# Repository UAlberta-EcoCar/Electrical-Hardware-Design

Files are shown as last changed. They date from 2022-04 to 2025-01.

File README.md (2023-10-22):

# Electrical-2022-Design-Hardware
## Relay-Board - Nicholas Semmens
Contains the hardware design for the upcoming prototype vehicle

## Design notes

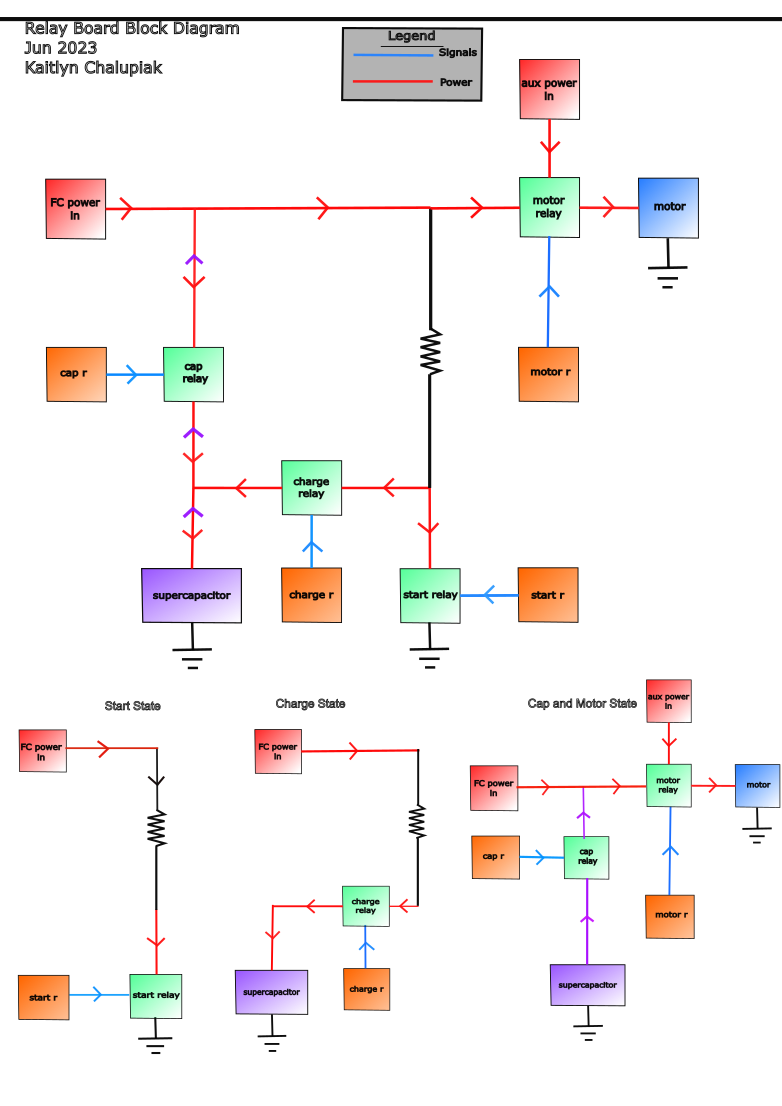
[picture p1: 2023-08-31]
Relay-Board_2023_Lucy_V1/Relay_Board_Lucy_V1/EcoCar_RelayBoard_BlockDiagram7_V3frfr.png

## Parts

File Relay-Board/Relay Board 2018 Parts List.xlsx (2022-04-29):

Relay Board Digikey List 2018
Part Description | Quantity | Store # | Store
8AWG Wire-to-Board Connector | 10 | 732-3204-ND
Switch (Voltage Divider) | 3 | EG1903-ND
Resistor 0603 (10.5k ohm) | 3 | P10.5KDBCT-ND
Resistor 0603 (768 ohm) | 3 | P768HCT-ND
Resistor 0603 (1.5k ohm) | 3 | P1.5KDBCT-ND
TVS Diode | 2 | P6KE15A-E3/54GICT-ND
RJ-11 | 3 | A119660-ND
RJ-45 | 2 | A122645-ND
Power Board Relay | 1 | CLA394-ND
Current Sensor (50A) | 2 | 620-1541-5-ND
Current Sensor (100A) | 1 | 620-1544-5-ND
Capacitor 0603 (0.1uF) | 3 | 399-1096-1-ND
Resistor 0603 (10k ohm) | 4 | RHM10KDCT-ND
Resistor 0603 (470 ohm) | 4 | RHM470DCT-ND
Photocoupler | 4 | H11L1-MQT-ND
P-MOS | 4 | DMP3056L-7DICT-ND
Flyback Diode | 4 | MUR420RLGOSCT-ND
Relay Socket | 4 | PB232-ND
90A Relay | 2 | 255-5246-ND

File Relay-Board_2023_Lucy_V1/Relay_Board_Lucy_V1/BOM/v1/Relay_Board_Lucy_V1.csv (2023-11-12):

Source: | C:\Users\Nicks_PC\Documents\virtDesk\Electrical-Hardware-Design\Relay-Board_2023_Lucy_V1\Relay_Board_Lucy_V1\Relay_Board_Lucy_V1.kicad_sch
Date: | 11/12/2023 2:34:30 PM
Tool: | Eeschema 7.0.2
Generator: | C:\Program Files\KiCad\7.0\bin\scripting\plugins/bom_csv_grouped_by_value.py
Component Count: | 113
Collated Components:
Item | Qty | Reference(s) | Value | LibPart | Footprint | Datasheet | DNP | Desc | Part#
1 | 17 | C1, C2, C5, C6, C7, C9, C10, C11, C13, C15, C16, C17, C19, C20, C21, C23, C24 | 100n | Device:C_Small | Capacitor_SMD:C_0603_1608Metric | https://datasheet.lcsc.com/lcsc/2304140030_FH--Guangdong-Fenghua-Advanced-Tech-0603B104K101NT_C88219.pdf |  |  | C88219
2 | 5 | C3, C4, C8, C14, C22 | 1u | Device:C_Small | Capacitor_SMD:C_0603_1608Metric | https://datasheet.lcsc.com/lcsc/2304140030_Murata-Electronics-GRM188R71C105KE15D_C77049.pdf |  |  | C77049
3 | 2 | C12, C18 | 4u7 | Device:C_Small | Capacitor_SMD:C_0603_1608Metric | https://datasheet.lcsc.com/lcsc/2304140030_FH--Guangdong-Fenghua-Advanced-Tech-0603B475K100NT_C108342.pdf |  | Desc: ESR < 1 | C108342
4 | 3 | D2, D10, D11 | AM23ESGW | Device:LED_Dual_AAK | Package_TO_SOT_SMD:SOT-23-3 | https://www.kingbrightusa.com/images/catalog/SPEC/AM23ESGW.pdf |  |  | 754-1634-6-ND
5 | 1 | D3 | STPS5045SG-TR | Device:D_Schottky_AKA | Package_TO_SOT_SMD:TO-263-2 | https://www.st.com/content/ccc/resource/technical/document/datasheet/65/29/29/69/d0/df/47/9c/DM00049255.pdf/files/DM00049255.pdf/jcr:content/translations/en.D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 |  |  | 497-13279-1-ND
6 | 6 | D4, D5, D6, D7, D8, D9 | BZX84-C3V3,215 | Device:D_Zener_Dual_CommonCathode_AAK | Package_TO_SOT_SMD:SOT-23-3 | https://assets.nexperia.com/documents/data-sheet/BZX84_SER.pdf |  |  | C85087
7 | 4 | D12, D13, D14, D15 | SD0805S020S1R0 | Device:D_Schottky | Diode_SMD:D_0805_2012Metric_Pad1.15x1.40mm_HandSolder | https://datasheets.kyocera-avx.com/schottky.pdf |  |  | 478-7800-1-ND
8 | 1 | FB1 | 300R | Device:FerriteBead_Small | Inductor_SMD:L_1206_3216Metric | https://www.vishay.com/docs/34023/ilb1206.pdf |  |  | 541-2283-1-ND
9 | 4 | H1, H2, H3, H4 | MountingHole | Mechanical:MountingHole | MountingHole:MountingHole_3.2mm_M3 | ~ |  |  | N/A
10 | 2 | J1, J10 | STD_PWR_HEADER | RB_PARTS:STD_PWR_HEADER | RB_FTP:STD_PWR_HEADER | https://www.molex.com/pdm_docs/ps/PS-43045.pdf |  |  | WM1791-ND
11 | 4 | J2, J3, J4, J5 | VP0265540000G | RB_PARTS:VP0265540000G | RB_FTP:CONN_VP0265x4xxxxG_AMP | https://mm.digikey.com/Volume0/opasdata/d220001/medias/docus/3772/8VP0003.pdf |  |  | VP0265540000G-ND
12 | 1 | J7 | USB_B_Micro | Connector:USB_B_Micro | RB_FTP:USB_Micro-B_Wuerth_629105150521 | https://www.we-online.com/katalog/datasheet/629105150521.pdf |  |  | 732-5960-1-ND
13 | 1 | J9 | DE9_Receptacle_MountingHoles | Connector:DE9_Receptacle_MountingHoles | Connector_Dsub:DSUB-9_Female_Horizontal_P2.77x2.84mm_EdgePinOffset7.70mm_Housed_MountingHolesOffset9.12mm | ~ |  |  | N/A
14 | 1 | JP3 | SolderJumper_2_Open | Jumper:SolderJumper_2_Open | Jumper:SolderJumper-2_P1.3mm_Open_TrianglePad1.0x1.5mm | ~ |  |  | N/A
15 | 2 | K1, K2 | HE1AN-P-DC12V-Y5 | RB_PARTS:HE1AN-W-DC12V-Y6 | RB_FTP:HE1AN-P-DC12V-Y5 | https://api.pim.na.industrial.panasonic.com/file_stream/main/fileversion/276 |  |  | 255-2777-ND
16 | 2 | K3, K4 | J115F11CH12VDCS61.5 | RB_PARTS:T9AV5L12-12 | RB_FTP:J115F11CH12VDCS61.5 | http://www.te.com/commerce/DocumentDelivery/DDEController?Action=showdoc |  |  | 2449-J115F11CH12VDCS61.5-ND
17 | 1 | Q1 | SI2302A-TPMSCT-ND | Device:Q_NMOS_GSD | Package_TO_SOT_SMD:SOT-23-3 | https://www.mccsemi.com/pdf/Products/SI2302A(SOT-23).pdf |  |  | SI2302A-TPMSCT-ND
18 | 4 | Q2, Q3, Q6, Q7 | FMMT491ATA | Device:Q_NPN_BEC | Package_TO_SOT_SMD:SOT-23-3 | https://www.diodes.com/assets/Datasheets/FMMT491A.pdf |  |  | C110504
19 | 1 | R1 | 160 | Device:R_Small | Resistor_SMD:R_0603_1608Metric | ~ |  |  | C245189
20 | 2 | R2, R4 | 2.2M | Device:R_Small | Resistor_SMD:R_0603_1608Metric | https://datasheet.lcsc.com/lcsc/2208261700_VO-SCR0603F2M2_C5140271.pdf |  |  | C5140271
21 | 1 | R3 | 953k | Device:R_Small | Resistor_SMD:R_0603_1608Metric | https://www.yageo.com/upload/media/product/productsearch/datasheet/rchip/PYu-RC_Group_51_RoHS_L_12.pdf |  |  | 311-953KHRCT-ND
22 | 1 | R5 | 549k | Device:R_Small | Resistor_SMD:R_0603_1608Metric | https://www.yageo.com/upload/media/product/app/datasheet/rchip/pyu-rc_group_51_rohs_l.pdf |  |  | 311-549KHRCT-ND
23 | 1 | R6 | 11.5k | Device:R_Small | Resistor_SMD:R_0603_1608Metric | https://datasheet.lcsc.com/lcsc/2304140030_Walsin-Tech-Corp-WR06X1152FTL_C168277.pdf |  |  | C168277
24 | 4 | R7, R11, R12, R20 | 100k | Device:R_Small | Resistor_SMD:R_0603_1608Metric | https://datasheet.lcsc.com/lcsc/2211251200_Ever-Ohms-Tech-TR0603D100KP0550Z_C5250829.pdf |  |  | C5250829
25 | 1 | R8 | 150 | Device:R_Small | Resistor_SMD:R_0603_1608Metric | https://datasheet.lcsc.com/lcsc/2206010130_UNI-ROYAL-Uniroyal-Elec-0603WAF1500T5E_C22808.pdf |  |  | C22808
26 | 3 | R9, R10, R19 | 417k | Device:R_Small | Resistor_SMD:R_0603_1608Metric | https://www.koaspeer.com/pdfs/RN73H.pdf |  |  | 2019-RN73H1JTTD4173C25CT-ND
27 | 3 | R13, R14, R17 | 50k | Device:R_Small | Resistor_SMD:R_0603_1608Metric | https://www.yageo.com/upload/media/product/productsearch/datasheet/rchip/PYu-RT_1-to-0.01_RoHS_L_15.pdf |  |  | 13-RT0603BRD0750KLCT-ND
28 | 3 | R15, R16, R18 | 200k | Device:R_Small | Resistor_SMD:R_0603_1608Metric | https://datasheet.lcsc.com/lcsc/2206010045_UNI-ROYAL-Uniroyal-Elec-0603WAF2003T5E_C25811.pdf |  |  | C25811
29 | 2 | R21, R23 | 140 | Device:R_Small | Resistor_SMD:R_0603_1608Metric | https://datasheet.lcsc.com/lcsc/2304140030_FH--Guangdong-Fenghua-Advanced-Tech-RS-03K1400FT_C304700.pdf |  |  | C304700
30 | 2 | R22, R24 | 130 | Device:R_Small | Resistor_SMD:R_0603_1608Metric | https://datasheet.lcsc.com/lcsc/2304140030_TA-I-Tech-RMS06FT1300_C209032.pdf |  |  | C209032
31 | 1 | R25 | 10k | Device:R_Small | Resistor_SMD:R_0603_1608Metric | https://datasheet.lcsc.com/lcsc/2206010045_UNI-ROYAL-Uniroyal-Elec-0603WAF1002T5E_C25804.pdf |  |  | C25804
32 | 4 | R27, R29, R31, R33 | 249 | Device:R_Small | Resistor_SMD:R_0603_1608Metric | https://datasheet.lcsc.com/lcsc/2304140030_Viking-Tech-ARG03FTC2490_C217903.pdf |  |  | C217903
33 | 1 | R34 | 120 | Device:R_Small | Resistor_SMD:R_0603_1608Metric | https://datasheet.lcsc.com/lcsc/2206010130_UNI-ROYAL-Uniroyal-Elec-0603WAF1200T5E_C22787.pdf | DNP |  | C22787
34 | 4 | R35, R36, R37, R38 | 422 | Device:R_Small | Resistor_SMD:R_0603_1608Metric | https://datasheet.lcsc.com/lcsc/2206010130_UNI-ROYAL-Uniroyal-Elec-0603WAF2200T5E_C22962.pdf |  |  | C22962
35 | 2 | SW1, SW2 | PTS815 SJM 250 SMTR LFS | Switch:SW_Push_45deg | Button_Switch_SMD:SW_SPST_PTS810 | https://datasheet.lcsc.com/lcsc/2106070033_C-K-PTS815SJM250SMTRLFS_C2689510.pdf |  |  | C2689510
36 | 2 | TP1, TP2 | TestPoint_Alt | Connector:TestPoint_Alt | TestPoint:TestPoint_Pad_1.0x1.0mm | ~ |  |  | N/A
37 | 2 | U1, U6 | ACS770LCB-050U-PFF | Sensor_Current:ACS770xCB-050B-PFF | RB_FTP:Allegro_CB_PFF_Adjusted | https://www.allegromicro.com/~/media/Files/Datasheets/ACS770-Datasheet.ashx |  |  | 620-1542-5-ND
38 | 1 | U2 | ACS770LCB-050B-PFF | Sensor_Current:ACS770xCB-050B-PFF | RB_FTP:Allegro_CB_PFF_Adjusted | https://www.allegromicro.com/~/media/Files/Datasheets/ACS770-Datasheet.ashx |  |  | 620-1541-5-ND
39 | 1 | U3 | MAX14572 | FCC_PARTS:MAX14572 | Package_SO:TSSOP-14-1EP_4.4x5mm_P0.65mm | https://www.analog.com/media/en/technical-documentation/data-sheets/MAX14571-MAX14573.pdf |  |  | MAX14572EUD+TCT-ND
40 | 2 | U4, U5 | TSV914IPT | RB_PARTS:TSV914IPT | Package_SO:TSSOP-14_4.4x5mm_P0.65mm | https://www.st.com/content/ccc/resource/technical/document/datasheet/68/e5/70/49/1a/0d/47/dd/CD00127596.pdf/files/CD00127596.pdf/jcr:content/translations/en.C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 |  |  | C83262
41 | 1 | U7 | LD39050PU33R | FCC_PARTS:LD39050PU33R | Package_DFN_QFN:DFN-6-1EP_3x3mm_P0.95mm_EP1.7x2.6mm | https://www.st.com/content/ccc/resource/technical/document/datasheet/12/43/cc/93/21/f6/41/66/CD00227527.pdf/files/CD00227527.pdf/jcr:content/translations/en.C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 |  |  | C132827
42 | 4 | U8, U11, U12, U13 | EL3H7(B)(TA)-VG | RB_PARTS:EL3H7(B)(TA)-VG | RB_FTP:SOIC_BTA-VG_EVS | https://everlightamericas.com/index.php?controller=attachment&id_attachment=2584 |  |  | C2891578
43 | 1 | U9 | MCP2542FD-E/SN | FCC_PARTS:MCP2542FD | Package_SO:SOIC-8_3.9x4.9mm_P1.27mm | https://ww1.microchip.com/downloads/aemDocuments/documents/APID/ProductDocuments/DataSheets/MCP2542FD-MCP2542WFD-4WFD-Data-Sheet-DS20005514C.pdf |  |  | C220598
44 | 1 | U10 | STM32F446RETx | MCU_ST_STM32F4:STM32F446RETx | Package_QFP:LQFP-64_10x10mm_P0.5mm | https://www.st.com/resource/en/datasheet/stm32f446re.pdf |  |  | C69336
45 | 1 | X1 | OXETDLJANF-8MHZ | RB_PARTS:OXETDLJANF-8MHZ | Crystal:Crystal_SMD_3225-4Pin_3.2x2.5mm | https://datasheet.lcsc.com/lcsc/2304140030_TAITIEN-Elec-OXETDLJANF-8-000000MHZ_C558766.pdf |  | 3.3V ±25ppm 8MHz SMD3225-4P Oscillators ROHS | C558766

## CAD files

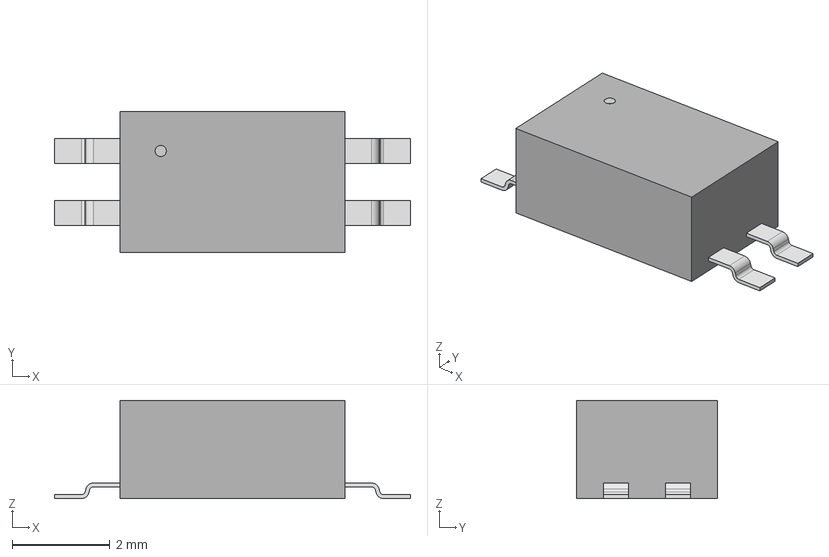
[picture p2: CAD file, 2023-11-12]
Relay-Board_2023_Lucy_V1/Relay_Board_Lucy_V1/SYM&FTP/3D/SOIC__B__TA_-VG_EVS.step
7.29 x 2.90 x 2.01 mm

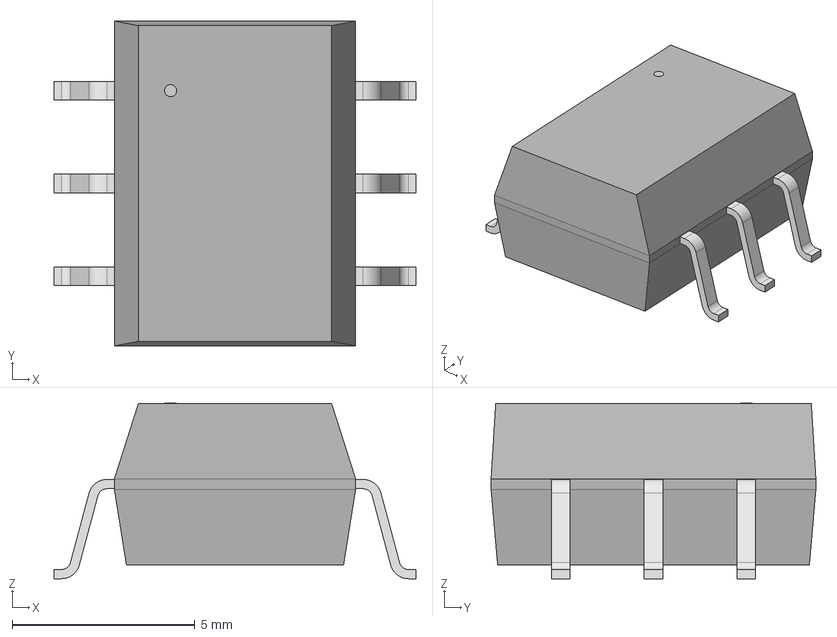
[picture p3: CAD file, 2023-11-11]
Relay-Board_2023_Lucy_V1/Relay_Board_Lucy_V1/SYM&FTP/3D/PDIP6_646BY_ONS.step
9.91 x 8.89 x 4.80 mm

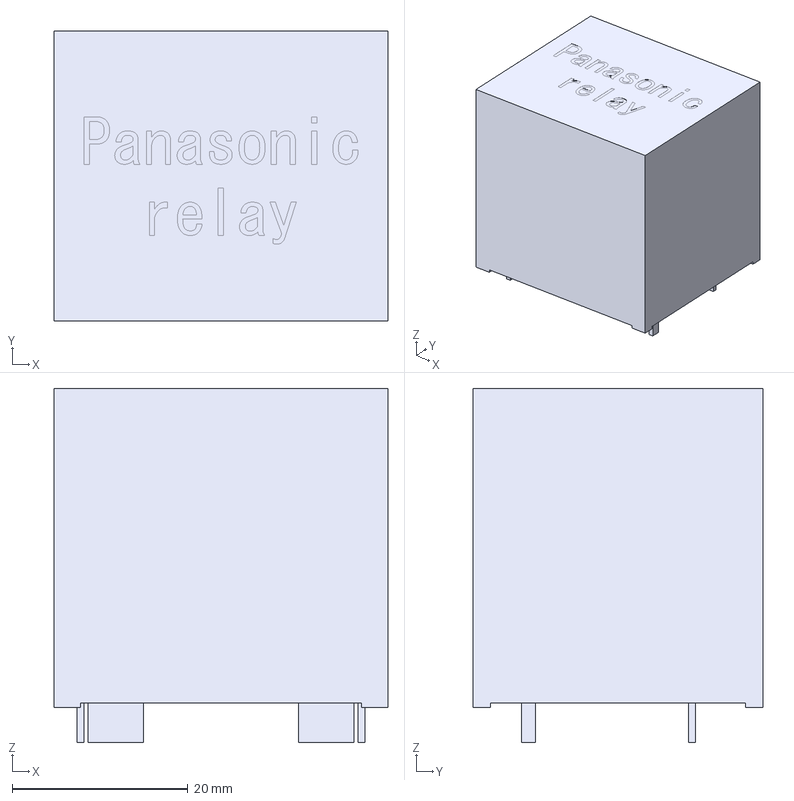
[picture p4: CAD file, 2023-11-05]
Relay-Board_2023_Lucy_V1/Relay_Board_Lucy_V1/SYM&FTP/3D/ahe32x5n.step
38.0 x 33.0 x 40.3 mm

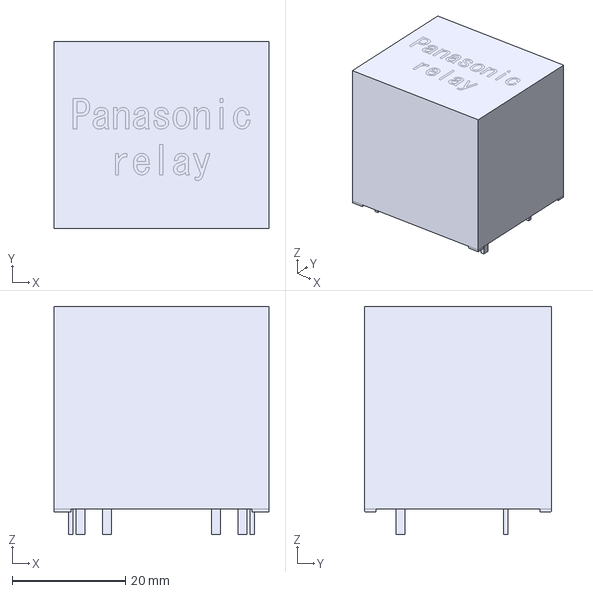
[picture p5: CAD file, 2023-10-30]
Relay-Board_2023_Lucy_V1/Relay_Board_Lucy_V1/SYM&FTP/3D/ahe4291.step
38.0 x 33.0 x 40.3 mm

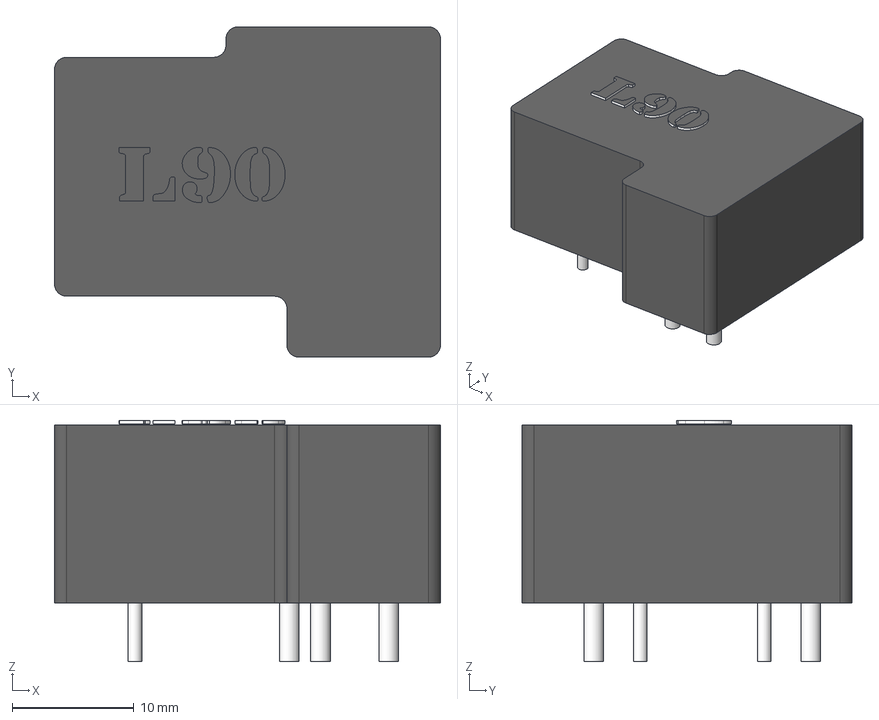
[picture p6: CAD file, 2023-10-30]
Relay-Board_2023_Lucy_V1/Relay_Board_Lucy_V1/SYM&FTP/3D/PTRH.step
31.7 x 27.1 x 19.8 mm

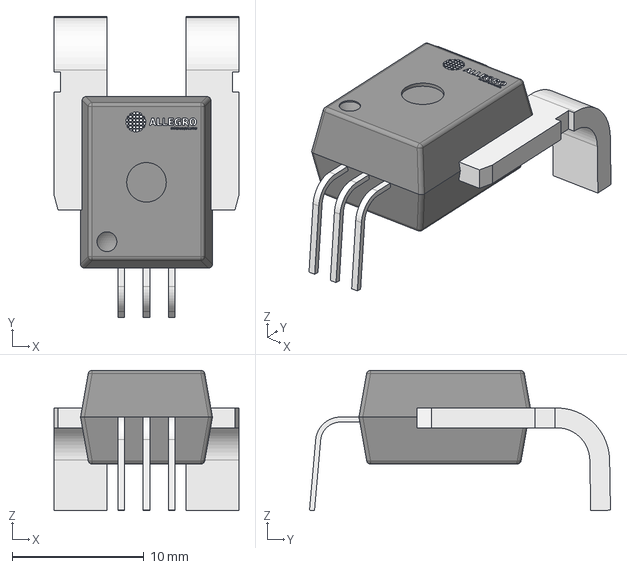
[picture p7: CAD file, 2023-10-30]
Relay-Board_2023_Lucy_V1/Relay_Board_Lucy_V1/SYM&FTP/3D/Allegro_MicroSystems_LLC_-_ACS770LCB-050U-PFF-T.step
14.0 x 22.8 x 10.6 mm

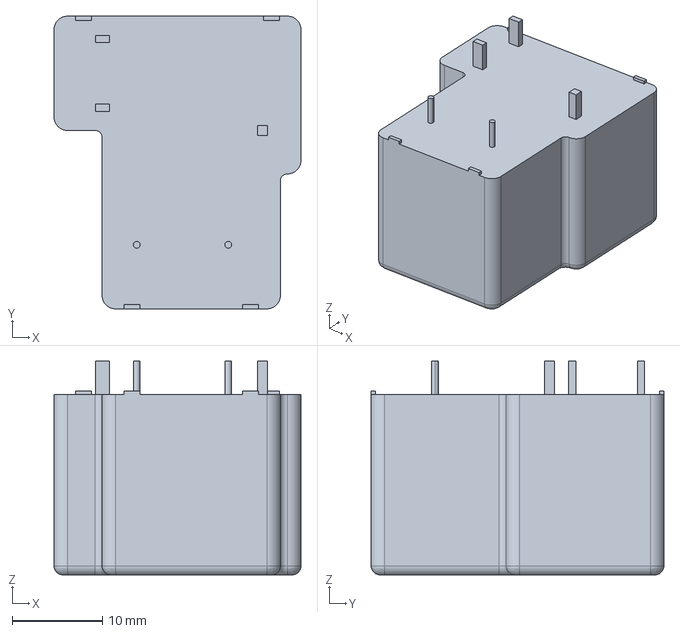
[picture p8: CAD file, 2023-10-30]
Relay-Board_2023_Lucy_V1/Relay_Board_Lucy_V1/SYM&FTP/3D/c-1423091-6-k-3d.stp
27.4 x 32.5 x 23.7 mm

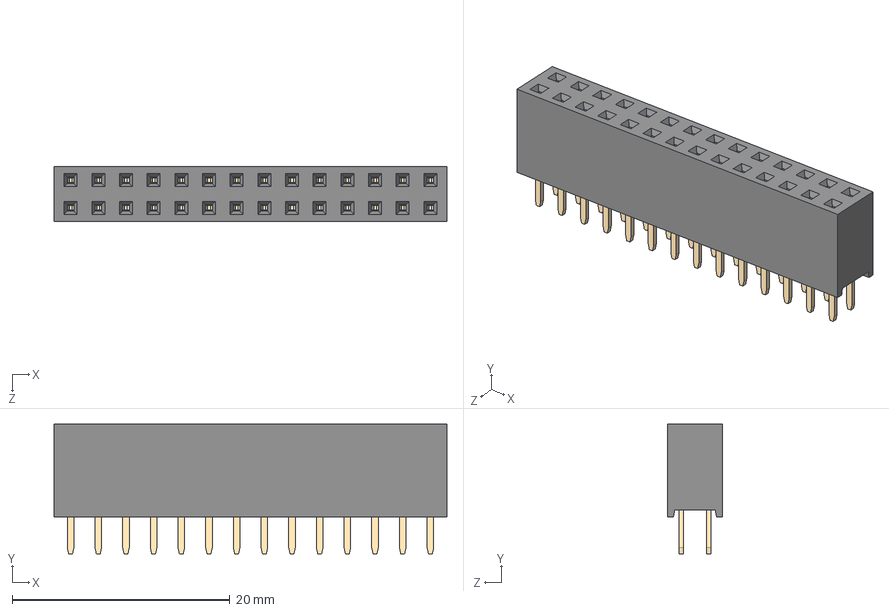
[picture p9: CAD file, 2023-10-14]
Relay-Board_2023_Lucy_V1/Relay_Board_Lucy_V1/SYM&FTP/3D/PPPC142LFBN-RC.STEP
36.1 x 11.9 x 5.08 mm
2 row tin body_14
2 row tin pins x 14

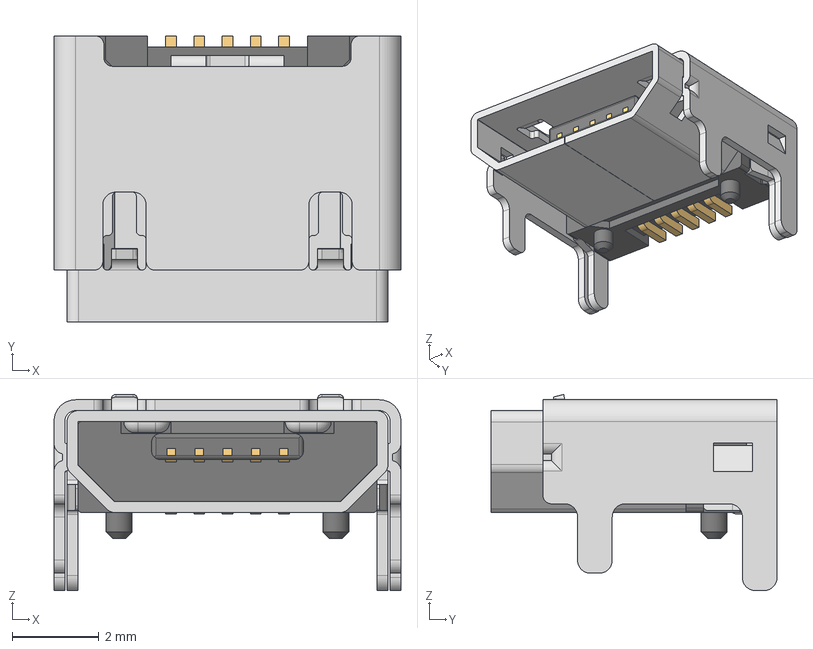
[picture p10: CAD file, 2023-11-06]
Relay-Board_2023_Lucy_V1/Relay_Board_Lucy_V1/SYM&FTP/3D/629105150521_Download_STP_629105150521_rev1.stp
8.00 x 6.60 x 4.52 mm
629105150521_Housing
629105150521_Pin1 x 4
629105150521_Pin2
629105150521_Shielding2
629105150521_Shielding

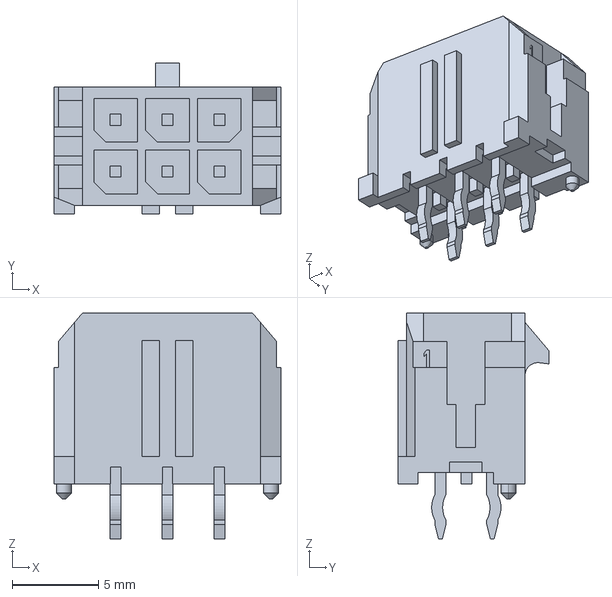
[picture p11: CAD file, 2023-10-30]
Relay-Board_2023_Lucy_V1/Relay_Board_Lucy_V1/SYM&FTP/3D/430450612.stp
13.2 x 8.77 x 13.1 mm

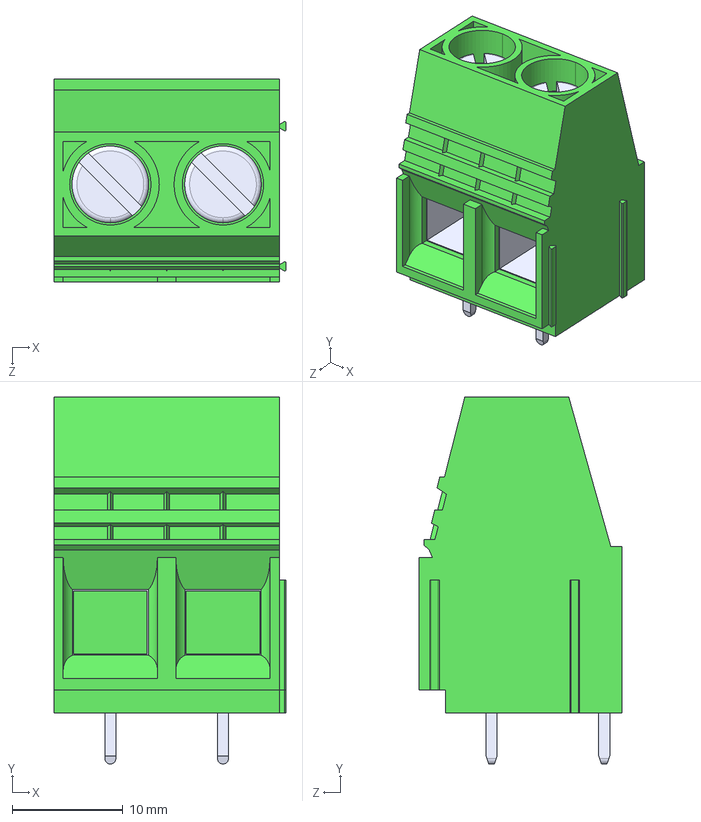
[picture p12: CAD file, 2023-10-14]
Relay-Board_2023_Lucy_V1/Relay_Board_Lucy_V1/SYM&FTP/3D/VP0265540000G.STEP
20.9 x 33.1 x 18.3 mm

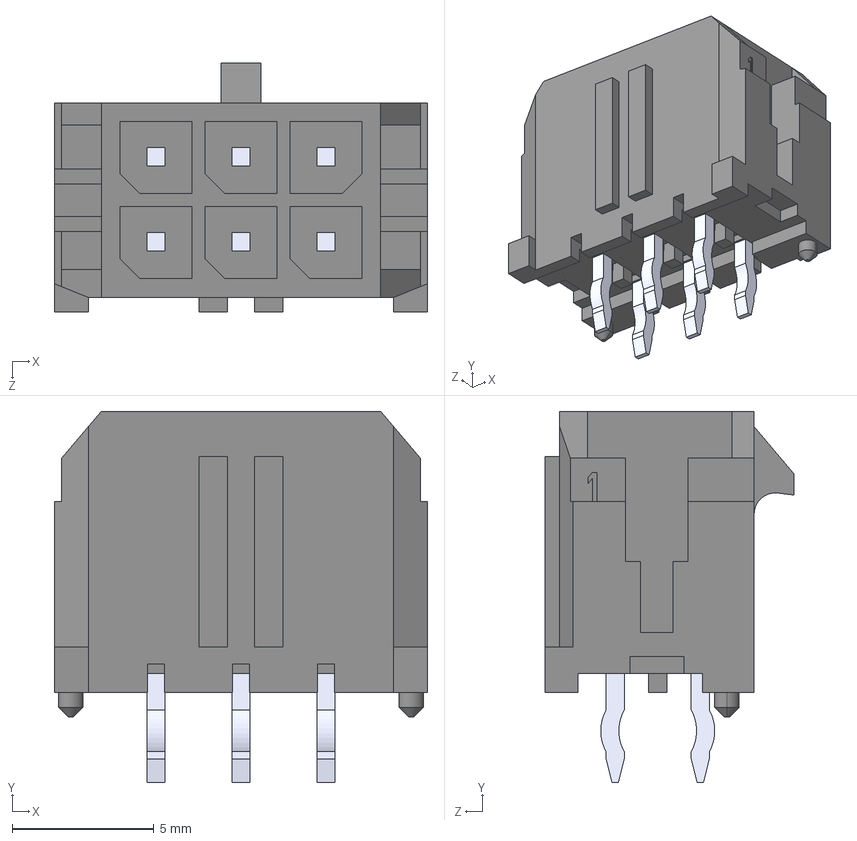
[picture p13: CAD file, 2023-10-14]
Relay-Board_2023_Lucy_V1/Relay_Board_Lucy_V1/SYM&FTP/3D/0430450612.step
13.2 x 13.1 x 8.77 mm

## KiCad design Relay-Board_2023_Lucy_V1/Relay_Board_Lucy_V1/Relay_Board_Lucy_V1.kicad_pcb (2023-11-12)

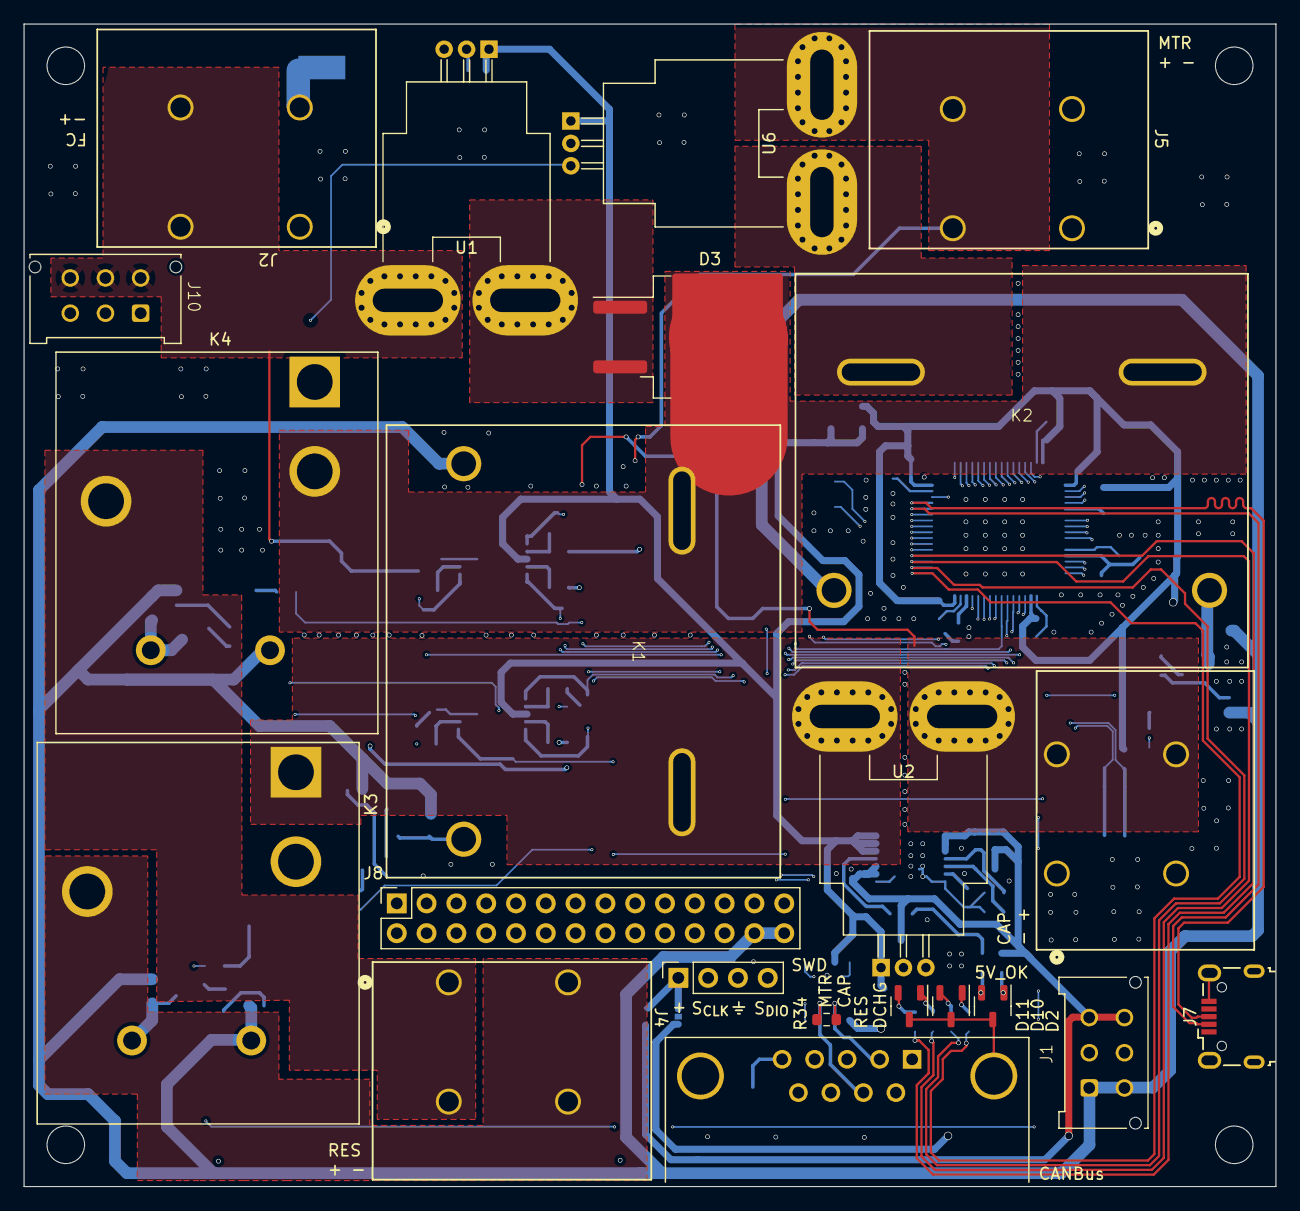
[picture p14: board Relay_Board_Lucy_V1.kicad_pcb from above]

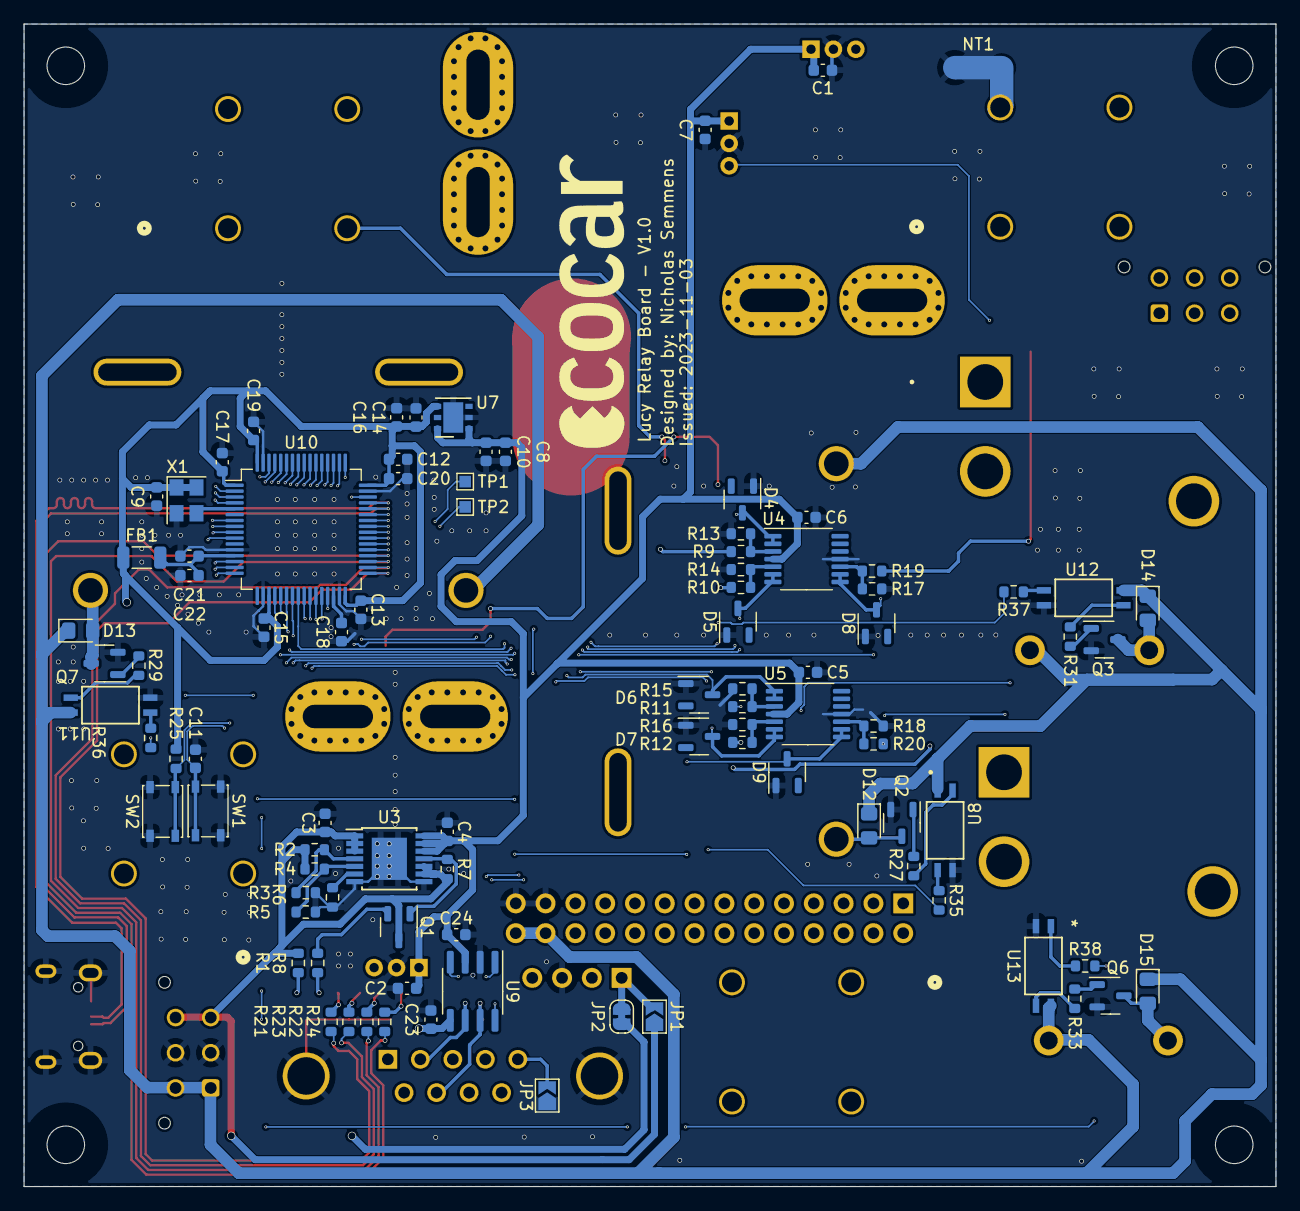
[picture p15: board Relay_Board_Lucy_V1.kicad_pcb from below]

Board: 4 copper layers, 106.7 x 99.1 mm, 118 parts (92 on the bottom side), 106 nets.

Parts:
C1, C2, C5, C6, C7, C9, C10, C11, C13, C15, C16, C17, C19, C20, C21, C23, C24: 100n; C_0603_1608Metric
C3, C4, C8, C14, C22: 1u; C_0603_1608Metric
C12, C18: 4u7; C_0603_1608Metric
D2, D10, D11: AM23ESGW; SOT-23-3
D3: STPS5045SG-TR; TO-263-2
D4, D5, D6, D7, D8, D9: BZX84-C3V3,215; SOT-23-3
D12, D13, D14, D15: SD0805S020S1R0; D_0805_2012Metric_Pad1.15x1.40mm_HandSolder
FB1: 300R; L_1206_3216Metric
H1, H2, H3, H4: MountingHole; MountingHole_3.2mm_M3
J1, J10: STD_PWR_HEADER
J2, J3, J4, J5: VP0265540000G; CONN_VP0265x4xxxxG_AMP
J6: SWD_HEADER; PinSocket_1x04_P2.54mm_Vertical
J7: USB_B_Micro; USB_Micro-B_Wuerth_629105150521
J8: Conn_02x14_Top_Bottom; PinSocket_2x14_P2.54mm_Vertical
J9: DE9_Receptacle_MountingHoles; DSUB-9_Female_Horizontal_P2.77x2.84mm_EdgePinOffset7.70mm_H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
JP1, JP3: SolderJumper_2_Open; SolderJumper-2_P1.3mm_Open_TrianglePad1.0x1.5mm
JP2: SolderJumper_2_Bridged; SolderJumper-2_P1.3mm_Bridged_RoundedPad1.0x1.5mm
K1, K2: HE1AN-P-DC12V-Y5
K3, K4: J115F11CH12VDCS61.5
NT1: NetTie_2; NetTie-2_SMD_Pad2.0mm
Q1: SI2302A-TPMSCT-ND; SOT-23-3
Q2, Q3, Q6, Q7: FMMT491ATA; SOT-23-3
R1: 160; R_0603_1608Metric
R2, R4: 2.2M; R_0603_1608Metric
R3: 953k; R_0603_1608Metric
R5: 549k; R_0603_1608Metric
R6: 11.5k; R_0603_1608Metric
R7, R11, R12, R20: 100k; R_0603_1608Metric
R8: 150; R_0603_1608Metric
R9, R10, R19: 417k; R_0603_1608Metric
R13, R14, R17: 50k; R_0603_1608Metric
R15, R16, R18: 200k; R_0603_1608Metric
R21, R23: 140; R_0603_1608Metric
R22, R24: 130; R_0603_1608Metric
R25: 10k; R_0603_1608Metric
R27, R29, R31, R33: 246; R_0603_1608Metric
R34: 120; R_0603_1608Metric
R35, R36, R37, R38: 422; R_0603_1608Metric
SW1, SW2: PTS815 SJM 250 SMTR LFS; SW_SPST_PTS810
TP1, TP2: TestPoint_Alt; TestPoint_Pad_1.0x1.0mm
U1, U6: ACS770LCB-050U-PFF; Allegro_CB_PFF_Adjusted
U2: ACS770LCB-050B-PFF; Allegro_CB_PFF_Adjusted
U3: MAX14572; TSSOP-14-1EP_4.4x5mm_P0.65mm
U4, U5: TSV914IPT; TSSOP-14_4.4x5mm_P0.65mm
U7: LD39050PU33R; DFN-6-1EP_3x3mm_P0.95mm_EP1.7x2.6mm
U8, U11, U12, U13: EL3H7(B)(TA)-VG; SOIC_BTA-VG_EVS
U9: MCP2542FD-E/SN; SOIC-8_3.9x4.9mm_P1.27mm
U10: STM32F446RETx; LQFP-64_10x10mm_P0.5mm
X1: OXETDLJANF-8MHZ; Crystal_SMD_3225-4Pin_3.2x2.5mm

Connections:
+3.3VA: C21.1, C22.1, FB1.2, U10.13 (VDDA)
+3V3: C9.1, C12.1, C13.1, C14.1, C15.1, C16.1, C17.1, C19.1, C20.1, C23.1, FB1.1, JP2.1 (A), R25.1, U7.4 (VO), U9.5 (VIO), U10.1 (VBAT), U10.19 (VDD), U10.32 (VDD), U10.48 (VDD), U10.64 (VDD), X1.1 (Tri-State), X1.4 (VDD)
+5V: C1.1, C2.1, C4.2, C5.1, C6.1, C7.1, C8.1, C10.1, C24.2, U1.1 (VCC), U2.1 (VCC), U3.12 (OUT), U3.13 (OUT), U3.14 (OUT), U4.4 (VCC+), U5.4 (VCC+), U6.1 (VCC), U7.1 (EN), U7.6 (VI), U9.3 (VDD)
/CAP Relay/V_{E}: R27.1, U8.3
/CAP+: J3.3, J3.4, R10.2, U2.4 (IP+)
/CAP_CURR: R12.2, U2.3 (VIOUT)
/FC+: J2.3, J2.4, J10.4 (12V), J10.5 (GND), J10.6 (5V), R19.2, U1.4 (IP+)
/FC_CURR: R11.2, U1.3 (VIOUT)
/MAIN_POWER_BUS: D3.2 (K), K1.1 (IN-), K2.4 (IN+), K4.2
/MCU/BOOT0: R25.2, SW2.2, U10.60 (BOOT0)
/MCU/CAN_H: J9.7, R34.2, U9.7 (CANH)
/MCU/CAN_L: J9.2, R34.1, U9.6 (CANL)
/MCU/CLK: U10.5 (PH0), X1.3 (OUT)
/MCU/PA0: J8.4, U10.14 (PA0)
/MCU/PA1: J8.2, U10.15 (PA1)
/MCU/PA2: J8.1, U10.16 (PA2)
/MCU/PA4: D8.3 (K), U4.8 (OUT3), U4.9 (IN3-), U10.20 (PA4)
/MCU/PA5: D9.3 (K), U5.8 (OUT3), U5.9 (IN3-), U10.21 (PA5)
/MCU/PA6: D5.3 (K), U4.6 (IN2-), U4.7 (OUT2), U10.22 (PA6)
/MCU/PA7: D7.3 (K), U5.6 (IN2-), U5.7 (OUT2), U10.23 (PA7)
/MCU/PA8: TP1.1, U10.41 (PA8)
/MCU/PA9: J8.21, U10.42 (PA9)
/MCU/PA10: J8.24, U10.43 (PA10)
/MCU/PA13: J6.4, U10.46 (PA13)
/MCU/PA14: J6.2, U10.49 (PA14)
/MCU/PA15: J8.17, U10.50 (PA15)
/MCU/PB0: R38.2, U10.26 (PB0)
/MCU/PB1: R37.2, U10.27 (PB1)
/MCU/PB2: R35.2, U10.28 (PB2)
/MCU/PB3: J8.14, U10.55 (PB3)
/MCU/PB4: J8.11, U10.56 (PB4)
/MCU/PB5: J8.12, U10.57 (PB5)
/MCU/PB6: J8.9, U10.58 (PB6)
/MCU/PB7: U9.8 (STBY), U10.59 (PB7)
/MCU/PB8: U9.4 (RXD), U10.61 (PB8)
/MCU/PB9: U9.1 (TXD), U10.62 (PB9)
/MCU/PB10: R36.2, U10.29 (PB10)
/MCU/PB12: R21.1, U10.33 (PB12)
/MCU/PB13: R22.2, U10.34 (PB13)
/MCU/PB14: R23.1, U10.35 (PB14)
/MCU/PB15: R24.2, U10.36 (PB15)
/MCU/PC0: J8.5, U10.8 (PC0)
/MCU/PC1: J8.6, U10.9 (PC1)
/MCU/PC2: J8.3, U10.10 (PC2)
/MCU/PC4: D4.3 (K), U4.1 (OUT1), U4.2 (IN1-), U10.24 (PC4)
/MCU/PC5: D6.3 (K), U5.1 (OUT1), U5.2 (IN1-), U10.25 (PC5)
/MCU/PC6: J8.20, U10.37 (PC6)
/MCU/PC7: J8.19, U10.38 (PC7)
/MCU/PC8: J8.22, U10.39 (PC8)
/MCU/PC9: TP2.1, U10.40 (PC9)
/MCU/PC10: J8.18, U10.51 (PC10)
/MCU/PC11: J8.15, U10.52 (PC11)
/MCU/PC12: J8.16, U10.53 (PC12)
/MCU/PC13: J8.10, U10.2 (PC13)
/MCU/PC14: J8.7, U10.3 (PC14)
/MCU/PC15: J8.8, U10.4 (PC15)
/MCU/PD2: J8.13, U10.54 (PD2)
/MCU/SHIELD: J9.5, JP3.2 (B)
/MCU/USB_D+: J7.3 (D+), U10.45 (PA12)
/MCU/USB_D-: J7.2 (D-), U10.44 (PA11)
/MCU/~RST: C11.1, SW1.2, U10.7 (NRST)
/MOTOR Relay/HIGH_VOLT_OUT: K2.1 (IN-), U6.4 (IP+)
/MOTOR Relay/V_{E}: R29.1, U11.3
/MOTOR+: J5.3, J5.4, R9.2, U6.5 (IP-)
/MOTOR_CURR: R20.2, U6.3 (VIOUT)
/RES+: J4.1, J4.2, K4.5
/RES-: J4.3, J4.4, K3.5
/TO_CAPS: K1.4 (IN+), K3.1, U2.5 (IP-)
/TO_LED: D2.1 (A1), R1.1
GNDA: C1.2, C2.2, C3.2, C4.1, C5.2, C6.2, C7.2, C8.2, C9.2, C10.2, C11.2, C12.2, C13.2, C14.2, C15.2, C16.2, C17.2, C18.2, C19.2, C20.2, C21.2, C22.2, C23.2, C24.1, D2.3 (K), D4.1 (A), D5.1 (A), D6.1 (A), D7.1 (A), D8.1 (A), D9.1 (A), D10.3 (K), D11.3 (K), J1.2 (GND), J1.5 (GND), J6.3, J7.5 (GND), J7.6 (Shield), J8.25, J8.27, J9.0 (PAD), JP3.1 (A), NT1.1, Q2.2 (E), Q3.2 (E), Q6.2 (E), Q7.2 (E), R3.1, R5.1, R6.1, R13.2, R14.2, R15.2, R16.2, R17.2, R18.2, SW1.1, SW2.1, U1.2 (GND), U2.2 (GND), U3.7 (GND), U3.8 (~HVEN), U3.15 (EP), U4.11 (VCC-), U5.11 (VCC-), U6.2 (GND), U7.2 (GND), U7.7 (GND), U8.2, U9.2 (VSS), U10.12 (VSSA), U10.18 (VSS), U10.31 (VSS), U10.47 (VSS), U10.63 (VSS), U11.2, U12.2, U13.2, X1.2 (GND)
GNDPWR: J2.1, J2.2, J3.1, J3.2, J5.1, J5.2, J10.1 (12V), J10.2 (GND), J10.3 (5V), K3.2, K4.1, NT1.2
unnamed: D2.2 (A2), R8.1
unnamed: D10.1 (A1), R21.2
unnamed: D10.2 (A2), R22.1
unnamed: D11.1 (A1), R23.2
unnamed: D11.2 (A2), R24.1
unnamed: D12.2 (A), K1.5 (CNTRL-), Q2.3 (C)
unnamed: D13.2 (A), K2.5 (CNTRL-), Q7.3 (C)
unnamed: D14.2 (A), K4.4, Q3.3 (C)
unnamed: D15.2 (A), K3.4, Q6.3 (C)
unnamed: J6.1, JP1.2 (B), JP2.2 (B)
unnamed: Q1.1 (G), R7.1, U3.11 (~FLAG)
unnamed: Q1.2 (S), R8.2
unnamed: Q2.1 (B), R27.2
unnamed: Q3.1 (B), R31.2
unnamed: Q6.1 (B), R33.2
unnamed: Q7.1 (B), R29.2
unnamed: R31.1, U12.3
unnamed: R33.1, U13.3
unnamed: R35.1, U8.1
unnamed: R36.1, U11.1
unnamed: R37.1, U12.1
unnamed: R38.1, U13.1
unnamed: D3.1 (A), D3.3 (A), U1.5 (IP-)
unnamed: R4.1, R5.2, U3.5 (OVLO)
unnamed: R6.2, U3.6 (SETI)
unnamed: R2.1, R3.2, U3.4 (UVLO)
unnamed: R9.1, R13.1, U4.3 (IN1+)
unnamed: R10.1, R14.1, U4.5 (IN2+)
unnamed: R17.1, R19.1, U4.10 (IN3+)
unnamed: R11.1, R15.1, U5.3 (IN1+)
unnamed: R12.1, R16.1, U5.5 (IN2+)
unnamed: R18.1, R20.1, U5.10 (IN3+)
unnamed: C18.1, U10.30 (VCAP_1)
UNPROTECTED_5V: C3.1, J1.3 (5V), J1.6 (5V), JP1.1 (A), Q1.3 (D), R1.2, R2.2, R4.2, R7.2, U3.1 (IN), U3.2 (IN), U3.3 (IN), U3.9 (RIEN), U3.10 (EN)
UNPROTECTED_12V: D12.1 (K), D13.1 (K), D14.1 (K), D15.1 (K), J1.1 (12V), J1.4 (12V), J8.26, J8.28, K1.6 (CNTRL+), K2.6 (CNTRL+), K3.3, K4.3, U8.4, U11.4, U12.4, U13.4

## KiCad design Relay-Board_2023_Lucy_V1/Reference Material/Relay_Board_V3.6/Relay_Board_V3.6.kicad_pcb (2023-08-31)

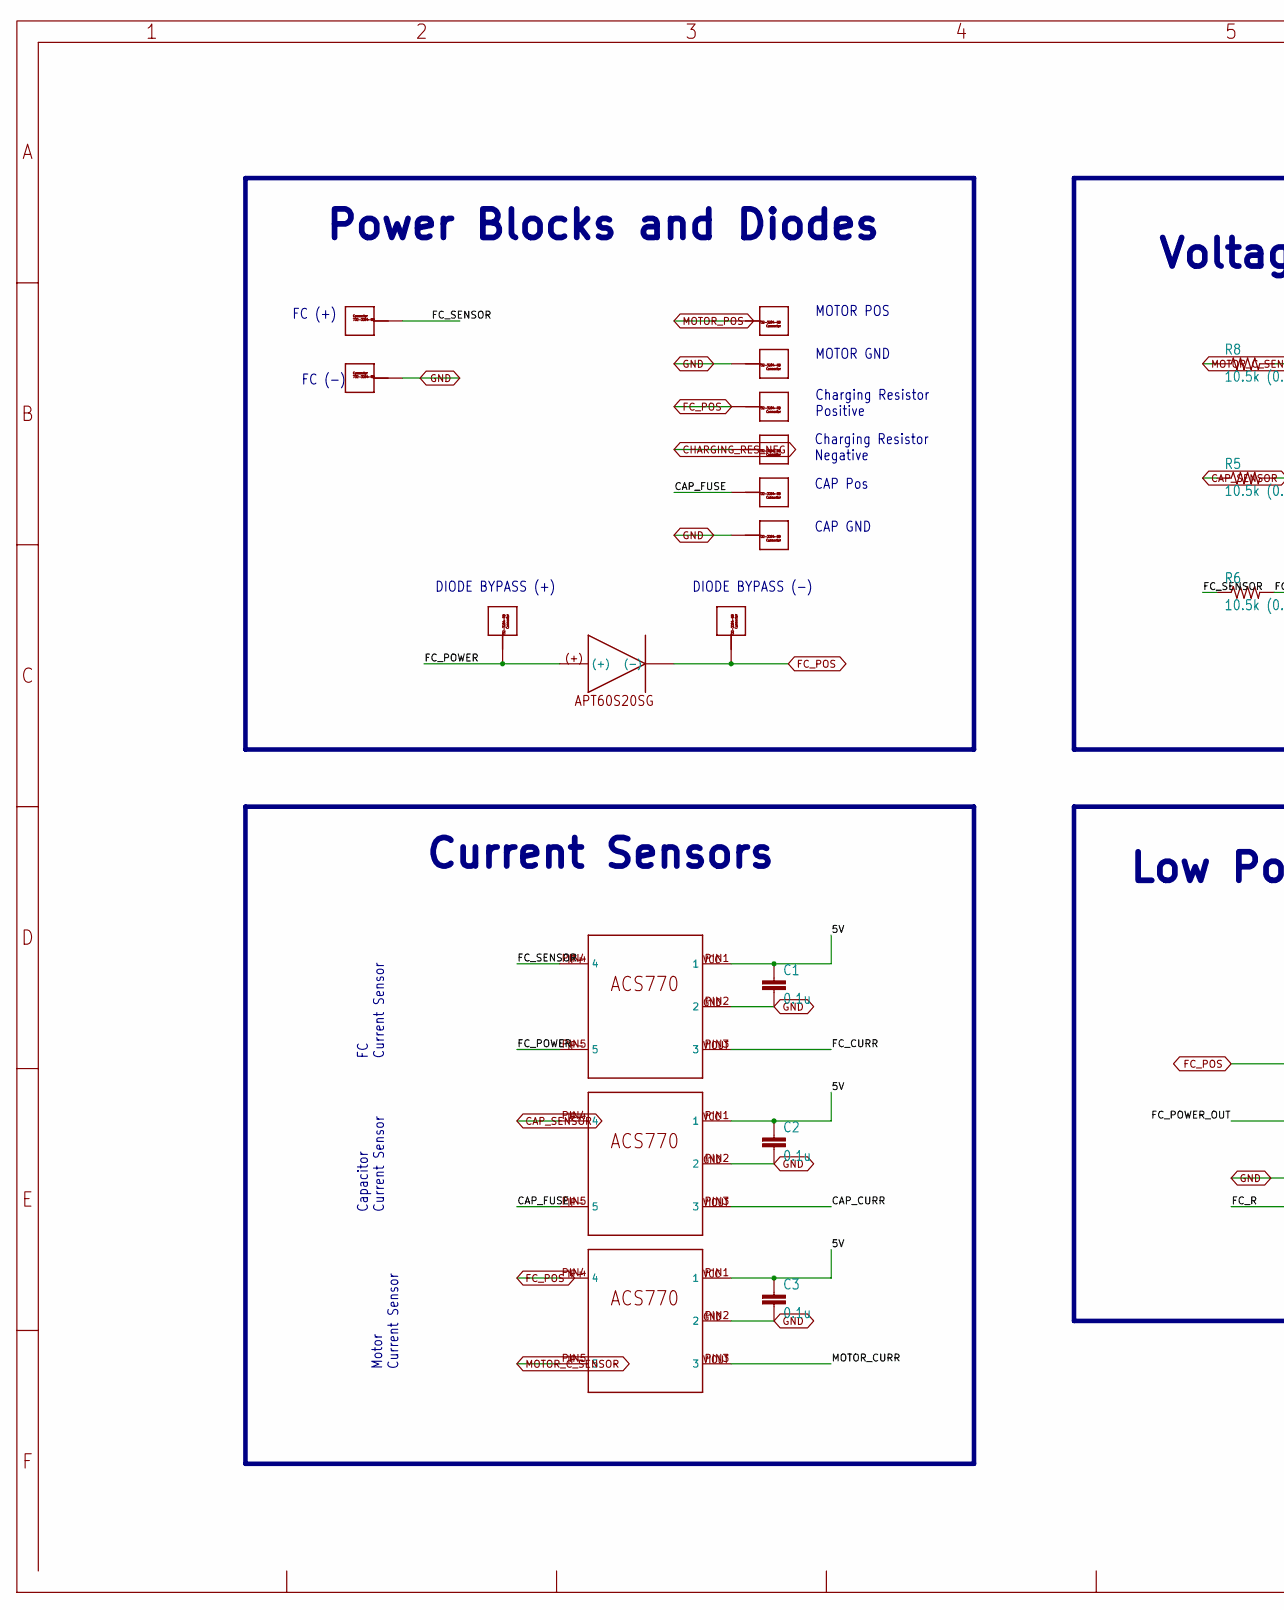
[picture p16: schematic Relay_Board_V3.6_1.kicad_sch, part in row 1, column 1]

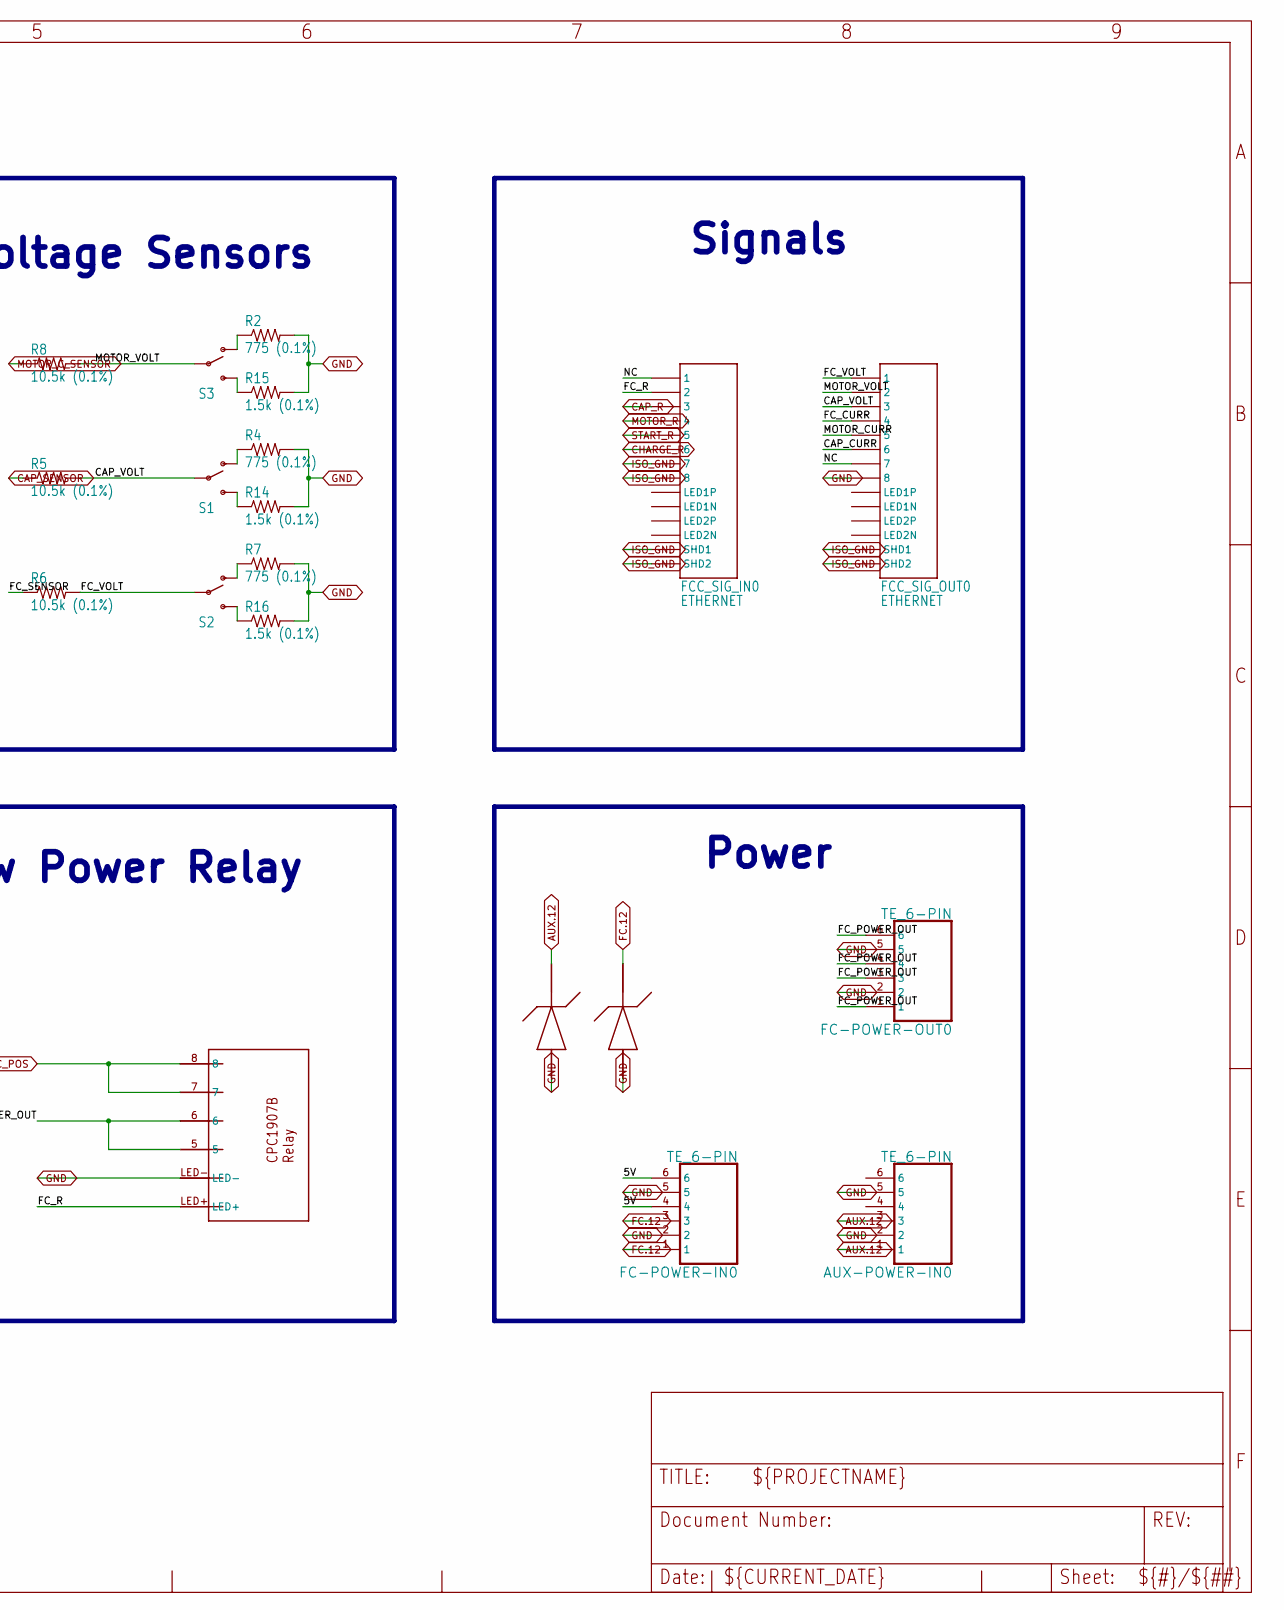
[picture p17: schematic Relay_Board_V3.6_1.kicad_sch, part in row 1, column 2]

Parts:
AUX-POWER-IN0: TE_6-PIN
C1, C2, C3: 0.1u; 0603-CAP
CAP.GND0, CAP.POS0, CAP.POS1, CAP.POS2: 732-3204-ND_CONNECTOR; 732-3204-ND
D1: APT60S20SG; TO268
FC-POWER-IN0: TE_6-PIN
FC-POWER-OUT0: TE_6-PIN
FC.GND0, FC.POS0: 732-3204-ND_CONNECTOR; 732-3204-ND
FCC_SIG_IN0: ETHERNET; A122645-ND
FCC_SIG_OUT0: ETHERNET; A122645-ND
FC_POWER_BOARD_RELAY0: RELAY-CPC1907B
MOTOR.GROUND0, MOTOR.POSITIVE0: 732-3204-ND_CONNECTOR; 732-3204-ND
R2, R4, R7: 775 (0.1%); R0805
R5, R6, R8: 10.5k (0.1%); R0805
R14, R15, R16: 1.5k (0.1%); R0805
RES.NEG0, RES.POS0: 732-3204-ND_CONNECTOR; 732-3204-ND
S1, S2, S3: SWITCH-SPDTPTH; SWITCH-SPDT
U$7, U$8, U$9: ACS770LCB_CURRENTSENSOR
U$15, U$16: P6KE15A-E3/54GICT-ND_TVS_DIODE; P6KE15A-E3_54GICT-ND_TVS_DIODE

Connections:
5V: C1.1, C2.1, C3.1, FC-POWER-IN0.4, FC-POWER-IN0.6, U$7.PIN1 (1), U$8.PIN1 (1), U$9.PIN1 (1)
AUX.12: AUX-POWER-IN0.1, AUX-POWER-IN0.3, U$16.P$2 (P(-)); also elsewhere on the board
CAP_CURR: FCC_SIG_OUT0.P$6 (6), U$8.PIN3 (3)
CAP_FUSE: CAP.POS0.P$1, CAP.POS0.P$2, CAP.POS0.P$3, CAP.POS0.P$4, CAP.POS0.P$5, CAP.POS0.P$6, CAP.POS0.P$7, CAP.POS0.P$8, CAP.POS0.P$9, CAP.POS0.P$10, U$8.PIN5 (5)
CAP_R: FCC_SIG_IN0.P$3 (3); also elsewhere on the board
CAP_SENSOR: R5.1, U$8.PIN4 (4); also elsewhere on the board
CAP_VOLT: FCC_SIG_OUT0.P$3 (3), R5.2, S1.2
CHARGE_R: FCC_SIG_IN0.P$6 (6); also elsewhere on the board
CHARGING_RES_NEG: RES.NEG0.P$1, RES.NEG0.P$2, RES.NEG0.P$3, RES.NEG0.P$4, RES.NEG0.P$5, RES.NEG0.P$6, RES.NEG0.P$7, RES.NEG0.P$8, RES.NEG0.P$9, RES.NEG0.P$10; also elsewhere on the board
FC.12: FC-POWER-IN0.1, FC-POWER-IN0.3, U$15.P$2 (P(-)); also elsewhere on the board
FC_CURR: FCC_SIG_OUT0.P$4 (4), U$7.PIN3 (3)
FC_POS: CAP.POS2.P$1, CAP.POS2.P$2, CAP.POS2.P$3, CAP.POS2.P$4, CAP.POS2.P$5, CAP.POS2.P$6, CAP.POS2.P$7, CAP.POS2.P$8, CAP.POS2.P$9, CAP.POS2.P$10, D1.(-), D1.C@1 ((-)), D1.C@2 ((-)), FC_POWER_BOARD_RELAY0.7, FC_POWER_BOARD_RELAY0.8, RES.POS0.P$1, RES.POS0.P$2, RES.POS0.P$3, RES.POS0.P$4, RES.POS0.P$5, RES.POS0.P$6, RES.POS0.P$7, RES.POS0.P$8, RES.POS0.P$9, RES.POS0.P$10, U$9.PIN4 (4); also elsewhere on the board
FC_POWER: CAP.POS1.P$1, CAP.POS1.P$2, CAP.POS1.P$3, CAP.POS1.P$4, CAP.POS1.P$5, CAP.POS1.P$6, CAP.POS1.P$7, CAP.POS1.P$8, CAP.POS1.P$9, CAP.POS1.P$10, D1.(+), U$7.PIN5 (5)
FC_POWER_OUT: FC-POWER-OUT0.1, FC-POWER-OUT0.3, FC-POWER-OUT0.4, FC-POWER-OUT0.6, FC_POWER_BOARD_RELAY0.5, FC_POWER_BOARD_RELAY0.6
FC_R: FCC_SIG_IN0.P$2 (2), FC_POWER_BOARD_RELAY0.LED+
FC_SENSOR: FC.POS0.P$1, FC.POS0.P$2, FC.POS0.P$3, FC.POS0.P$4, FC.POS0.P$5, FC.POS0.P$6, FC.POS0.P$7, FC.POS0.P$8, FC.POS0.P$9, FC.POS0.P$10, R6.1, U$7.PIN4 (4)
FC_VOLT: FCC_SIG_OUT0.P$1 (1), R6.2, S2.2
GND: AUX-POWER-IN0.2, AUX-POWER-IN0.5, C1.2, C2.2, C3.2, CAP.GND0.P$1, CAP.GND0.P$2, CAP.GND0.P$3, CAP.GND0.P$4, CAP.GND0.P$5, CAP.GND0.P$6, CAP.GND0.P$7, CAP.GND0.P$8, CAP.GND0.P$9, CAP.GND0.P$10, FC-POWER-IN0.2, FC-POWER-IN0.5, FC-POWER-OUT0.2, FC-POWER-OUT0.5, FC.GND0.P$1, FC.GND0.P$2, FC.GND0.P$3, FC.GND0.P$4, FC.GND0.P$5, FC.GND0.P$6, FC.GND0.P$7, FC.GND0.P$8, FC.GND0.P$9, FC.GND0.P$10, FCC_SIG_OUT0.P$8 (8), FC_POWER_BOARD_RELAY0.LED-, MOTOR.GROUND0.P$1, MOTOR.GROUND0.P$2, MOTOR.GROUND0.P$3, MOTOR.GROUND0.P$4, MOTOR.GROUND0.P$5, MOTOR.GROUND0.P$6, MOTOR.GROUND0.P$7, MOTOR.GROUND0.P$8, MOTOR.GROUND0.P$9, MOTOR.GROUND0.P$10, R2.2, R4.2, R7.2, R14.2, R15.2, R16.2, U$7.PIN2 (2), U$8.PIN2 (2), U$9.PIN2 (2), U$15.P$1 (P(+)), U$16.P$1 (P(+)); also elsewhere on the board
ISO_GND: FCC_SIG_IN0.P$7 (7), FCC_SIG_IN0.P$8 (8), FCC_SIG_IN0.P$13 (SHD1), FCC_SIG_IN0.P$14 (SHD2), FCC_SIG_OUT0.P$13 (SHD1), FCC_SIG_OUT0.P$14 (SHD2); also elsewhere on the board
MOTOR_CURR: FCC_SIG_OUT0.P$5 (5), U$9.PIN3 (3)
MOTOR_C_SENSOR: R8.1, U$9.PIN5 (5); also elsewhere on the board
MOTOR_POS: MOTOR.POSITIVE0.P$1, MOTOR.POSITIVE0.P$2, MOTOR.POSITIVE0.P$3, MOTOR.POSITIVE0.P$4, MOTOR.POSITIVE0.P$5, MOTOR.POSITIVE0.P$6, MOTOR.POSITIVE0.P$7, MOTOR.POSITIVE0.P$8, MOTOR.POSITIVE0.P$9, MOTOR.POSITIVE0.P$10; also elsewhere on the board
MOTOR_R: FCC_SIG_IN0.P$4 (4); also elsewhere on the board
MOTOR_VOLT: FCC_SIG_OUT0.P$2 (2), R8.2, S3.2
unnamed: R4.1, S1.1 (O)
unnamed: R14.1, S1.3 (S)
unnamed: R2.1, S3.1 (O)
unnamed: R15.1, S3.3 (S)
unnamed: R7.1, S2.1 (O)
unnamed: R16.1, S2.3 (S)
NC: FCC_SIG_IN0.P$1 (1), FCC_SIG_OUT0.P$7 (7)
START_R: FCC_SIG_IN0.P$5 (5); also elsewhere on the board

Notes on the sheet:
Power
Current Sensors
MOTOR GND
FC (+)
Charging Resistor Positive
Voltage Sensors
Motor Current Sensor
CAP Pos
MOTOR POS
CAP GND
DIODE BYPASS (+)
Charging Resistor Negative
Power Blocks and Diodes
Signals
Capacitor Current Sensor
Low Power Relay
FC (-)
DIODE BYPASS (-)
FC Current Sensor

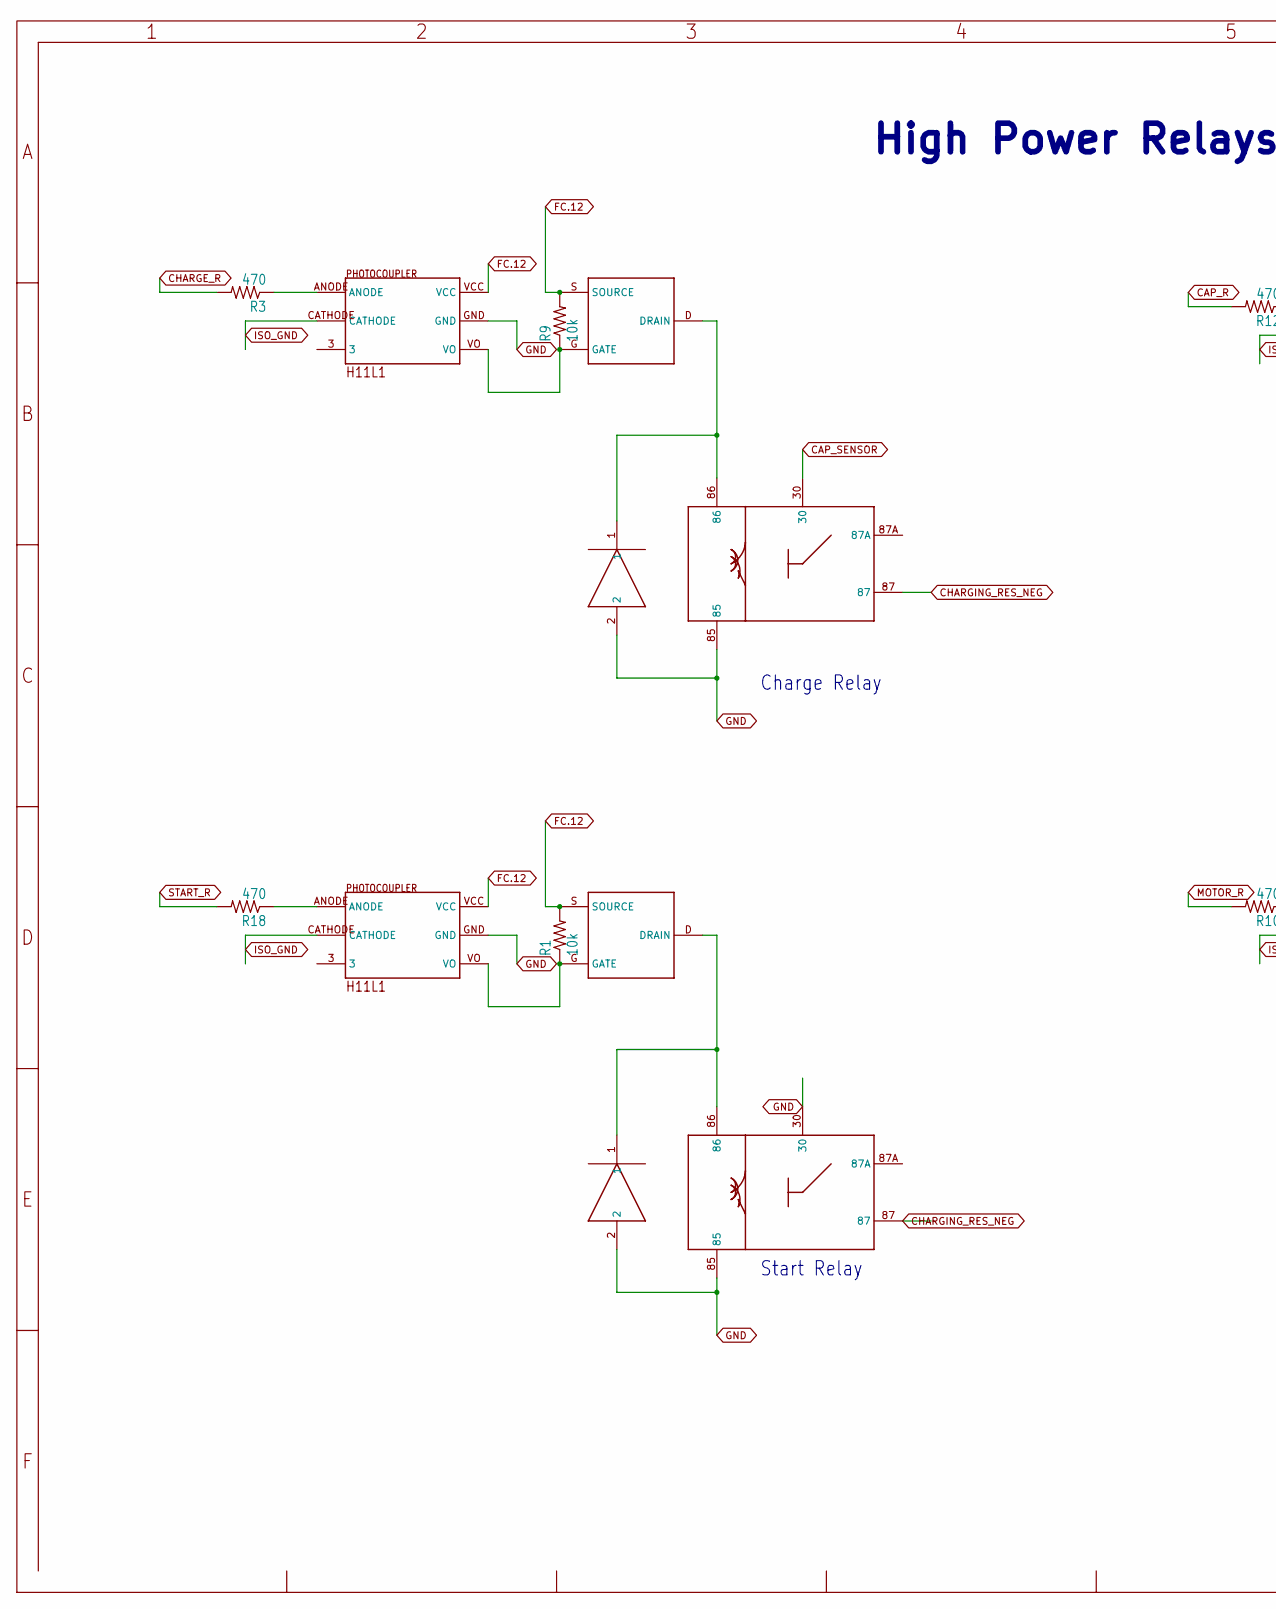
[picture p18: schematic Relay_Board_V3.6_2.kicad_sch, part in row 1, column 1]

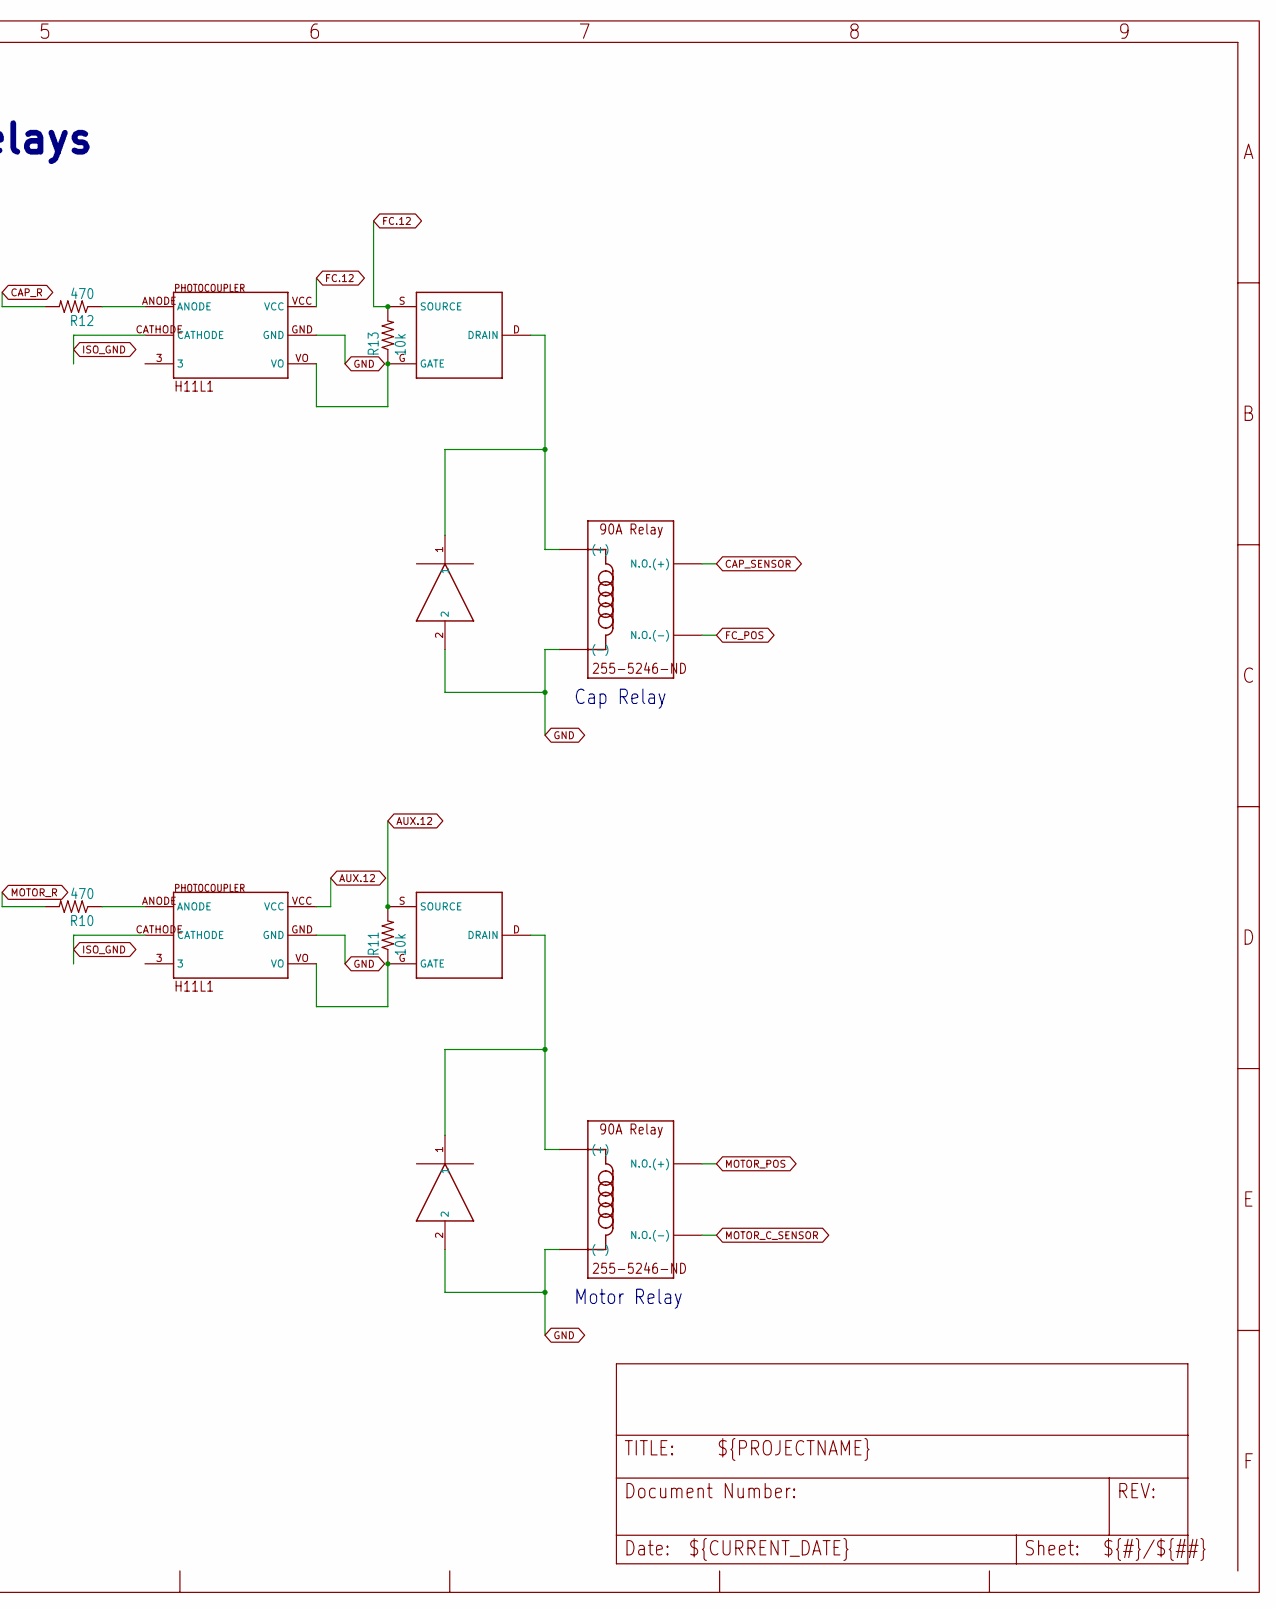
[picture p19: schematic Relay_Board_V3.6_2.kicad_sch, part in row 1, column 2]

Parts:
CR1, CR2, CR3, CR4: MUR420RLG; DO-201AD
R1, R9, R11, R13: 10k; 0603-RES
R3, R10, R12, R18: 470; 0603-RES
START.RELAY1, START.RELAY2: VCF4-1000
U$1, U$3, U$5, U$11: DMP3056L-7DMP3056L-7; DMP3056L-7
U$2, U$4, U$6, U$12: H11L1H11L1; H11L1
U$13, U$14: 255-5246-ND

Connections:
AUX.12: R11.2, U$3.S (SOURCE), U$4.VCC; also elsewhere on the board
CAP_R: R12.2; also elsewhere on the board
CAP_SENSOR: START.RELAY2.30, U$13.NO(+) (N.O.(+)), U$13.NO(++) (N.O.(+)); also elsewhere on the board
CHARGE_R: R3.2; also elsewhere on the board
CHARGING_RES_NEG: START.RELAY1.87, START.RELAY2.87; also elsewhere on the board
FC.12: R1.2, R9.2, R13.2, U$1.S (SOURCE), U$2.VCC, U$5.S (SOURCE), U$6.VCC, U$11.S (SOURCE), U$12.VCC; also elsewhere on the board
FC_POS: U$13.NO(-) (N.O.(-)), U$13.NO(--) (N.O.(-)); also elsewhere on the board
GND: CR1.2, CR2.2, CR3.2, CR4.2, START.RELAY1.30, START.RELAY1.85, START.RELAY2.85, U$2.GND, U$4.GND, U$6.GND, U$12.GND, U$13.(-), U$13.(--) ((-)), U$14.(-), U$14.(--) ((-)); also elsewhere on the board
ISO_GND: U$2.CATHODE, U$4.CATHODE, U$6.CATHODE, U$12.CATHODE; also elsewhere on the board
MOTOR_C_SENSOR: U$14.NO(-) (N.O.(-)), U$14.NO(--) (N.O.(-)); also elsewhere on the board
MOTOR_POS: U$14.NO(+) (N.O.(+)), U$14.NO(++) (N.O.(+)); also elsewhere on the board
MOTOR_R: R10.2; also elsewhere on the board
unnamed: R9.1, U$1.G (GATE), U$2.VO
unnamed: R3.1, U$2.ANODE
unnamed: CR2.1, START.RELAY2.86, U$1.D (DRAIN)
unnamed: R11.1, U$3.G (GATE), U$4.VO
unnamed: R10.1, U$4.ANODE
unnamed: CR3.1, U$3.D (DRAIN), U$14.(+), U$14.(++) ((+))
unnamed: R13.1, U$5.G (GATE), U$6.VO
unnamed: R12.1, U$6.ANODE
unnamed: CR4.1, U$5.D (DRAIN), U$13.(+), U$13.(++) ((+))
unnamed: R1.1, U$11.G (GATE), U$12.VO
unnamed: R18.1, U$12.ANODE
unnamed: CR1.1, START.RELAY1.86, U$11.D (DRAIN)
START_R: R18.2; also elsewhere on the board

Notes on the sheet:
Start Relay
Cap Relay
High Power Relays
Charge Relay
Motor Relay

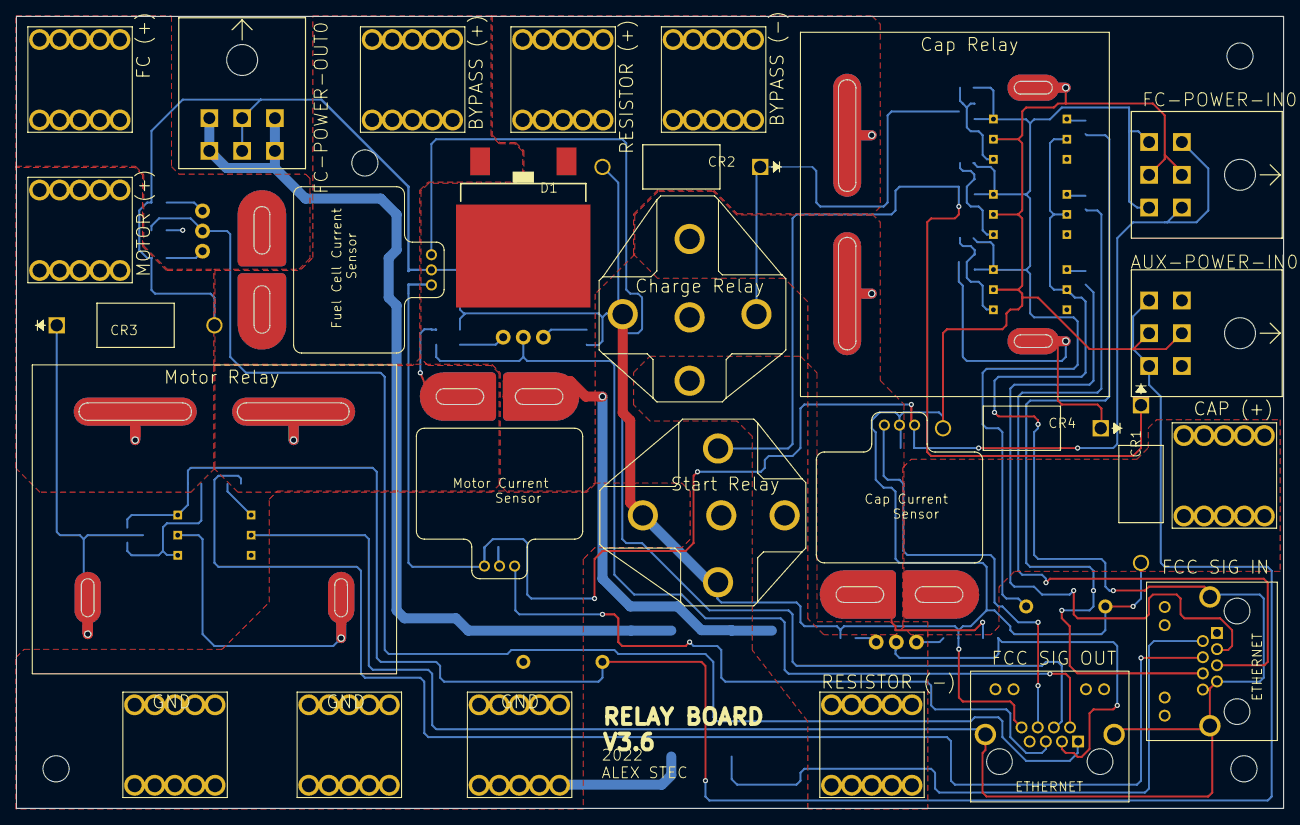
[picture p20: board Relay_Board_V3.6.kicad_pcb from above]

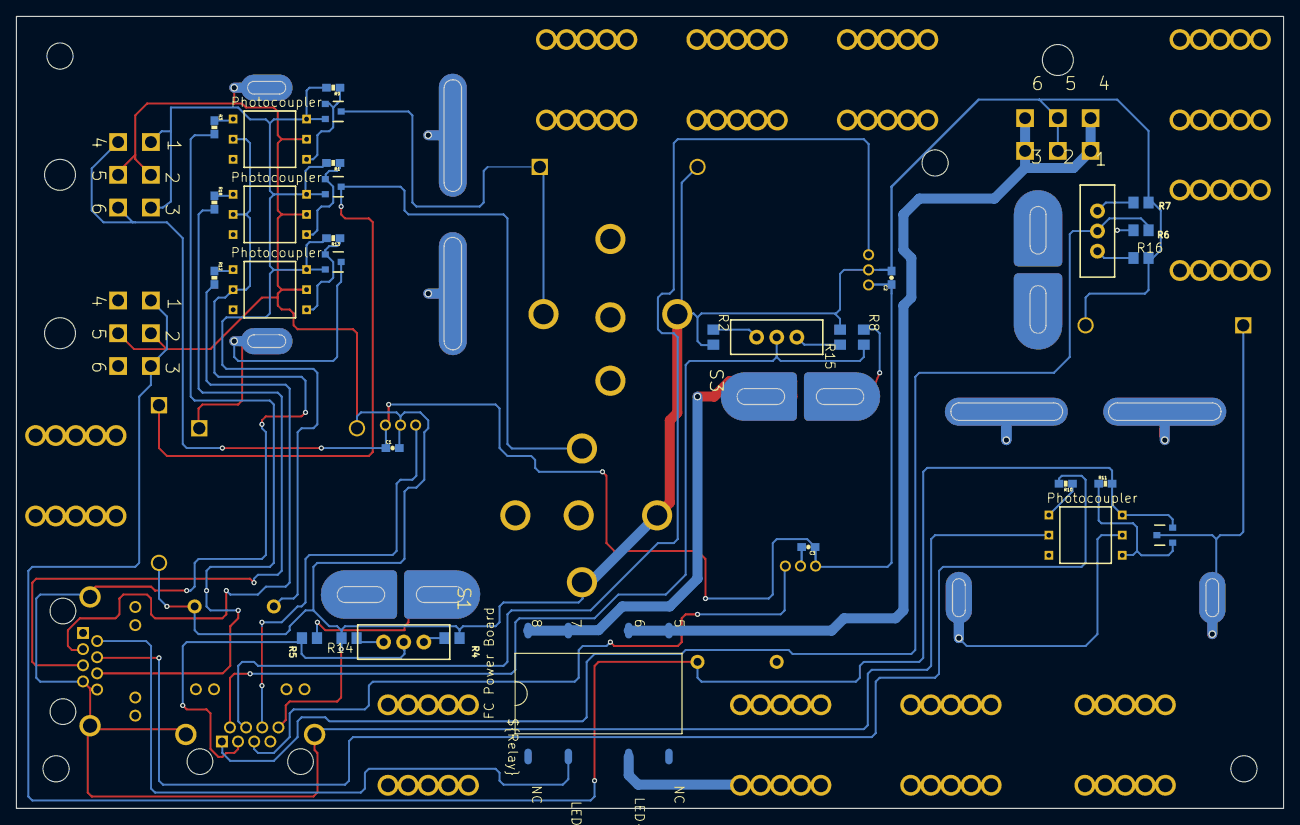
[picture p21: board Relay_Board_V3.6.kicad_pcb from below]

Board: 2 copper layers, 160.0 x 100.0 mm, 65 parts (32 on the bottom side), 44 nets.

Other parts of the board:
U$18, U$20, U$21, U$23: STAND-OFF

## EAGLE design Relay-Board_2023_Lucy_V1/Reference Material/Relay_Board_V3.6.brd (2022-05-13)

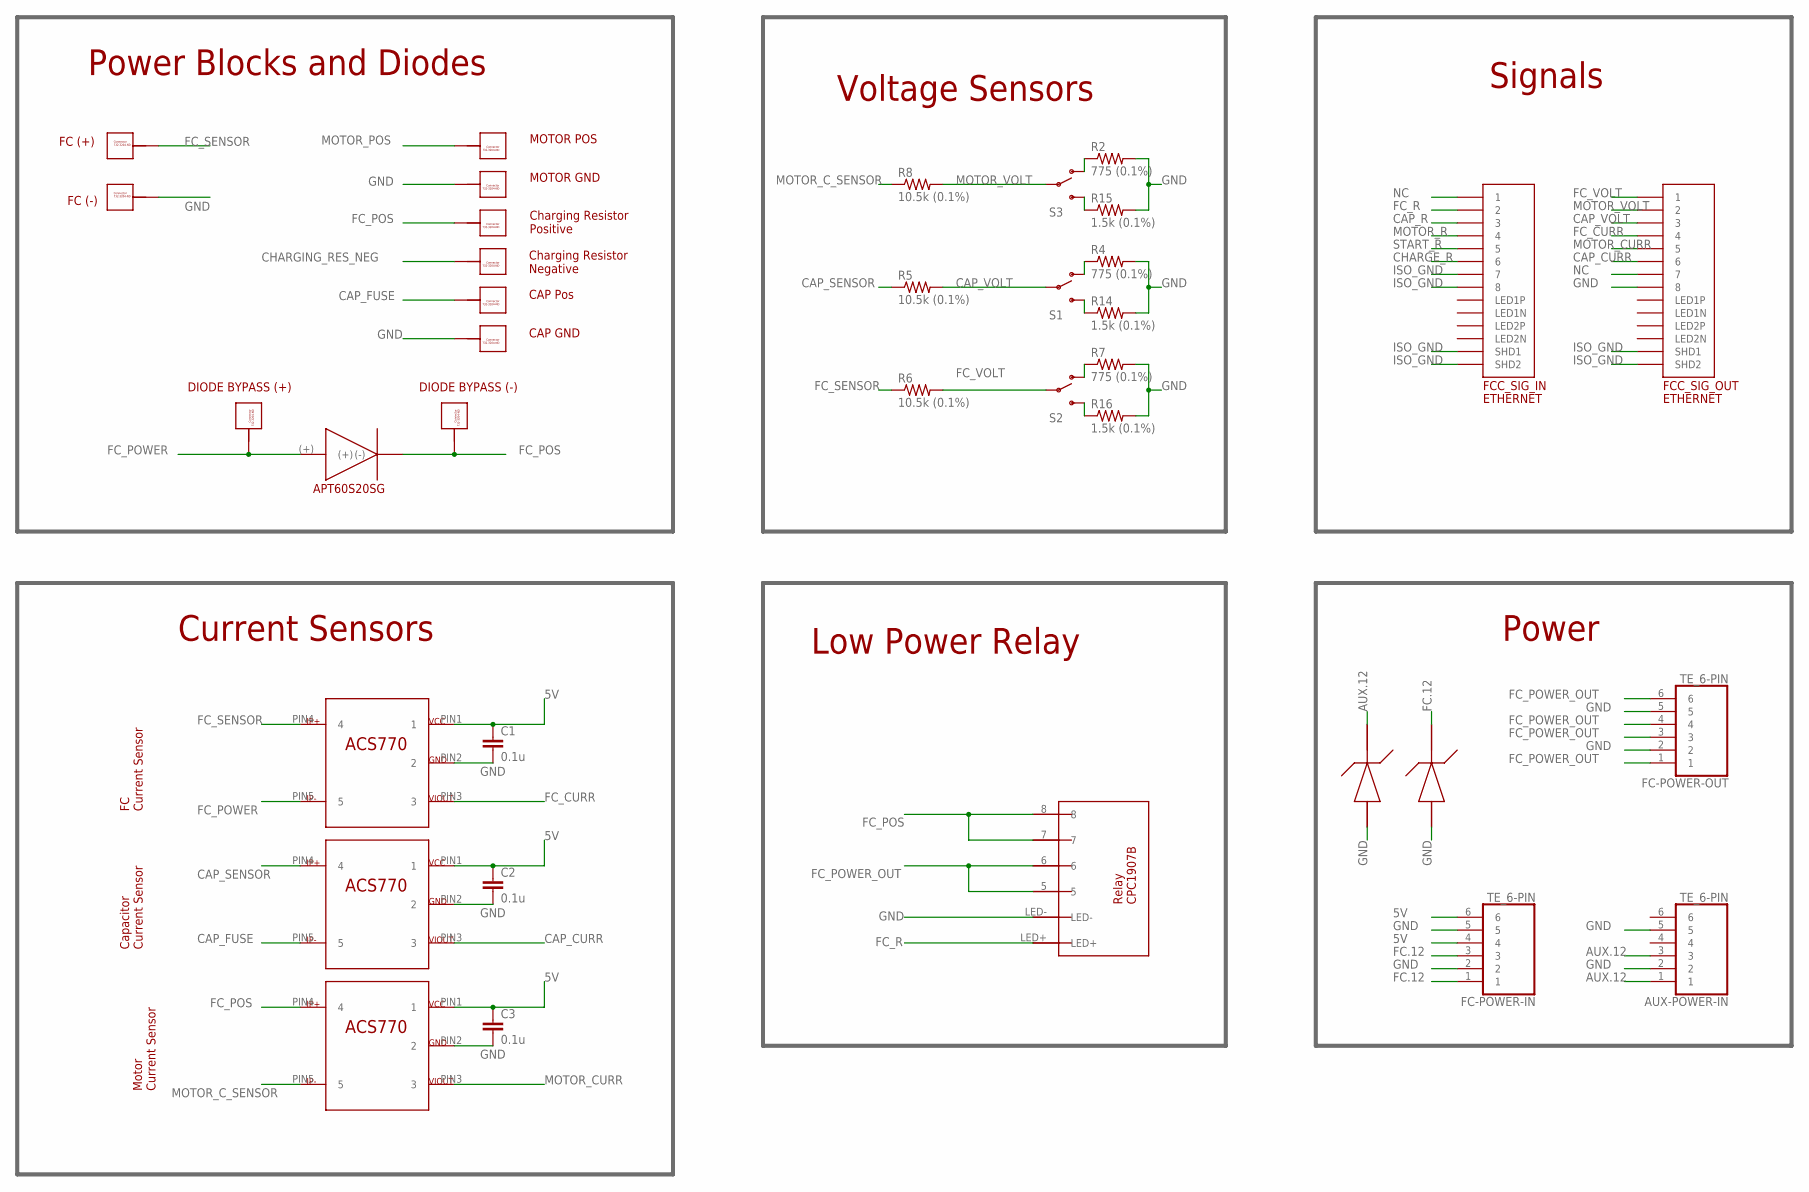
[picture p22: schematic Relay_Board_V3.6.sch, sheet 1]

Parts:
AUX-POWER-IN: TE_6-PIN
C1, C2, C3: 0.1u; 0603-CAP
CAP.GND, CAP.POS, CAP.POS1, CAP.POS2: 732-3204-ND_CONNECTOR; 732-3204-ND
D1: APT60S20SG; TO268
FC-POWER-IN: TE_6-PIN
FC-POWER-OUT: TE_6-PIN
FC.GND, FC.POS: 732-3204-ND_CONNECTOR; 732-3204-ND
FCC_SIG_IN: ETHERNET; A122645-ND
FCC_SIG_OUT: ETHERNET; A122645-ND
FC_POWER_BOARD_RELAY: RELAY-CPC1907B
MOTOR.GROUND, MOTOR.POSITIVE: 732-3204-ND_CONNECTOR; 732-3204-ND
R2, R4, R7: 775 (0.1%); R0805
R5, R6, R8: 10.5k (0.1%); R0805
R14, R15, R16: 1.5k (0.1%); R0805
RES.NEG, RES.POS: 732-3204-ND_CONNECTOR; 732-3204-ND
S1, S2, S3: SWITCH-SPDTPTH; SWITCH-SPDT
U$7, U$8, U$9: ACS770LCB_CURRENTSENSOR
U$15, U$16: P6KE15A-E3/54GICT-ND_TVS_DIODE

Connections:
5V: C1.1, C2.1, C3.1, FC-POWER-IN.4, FC-POWER-IN.6, U$7.PIN1 (1), U$8.PIN1 (1), U$9.PIN1 (1)
AUX.12: AUX-POWER-IN.1, AUX-POWER-IN.3, U$16.P$2 (P(-)); also elsewhere on the board
CAP_CURR: FCC_SIG_OUT.P$6 (6), U$8.PIN3 (3)
CAP_FUSE: CAP.POS.P$1, CAP.POS.P$2, CAP.POS.P$3, CAP.POS.P$4, CAP.POS.P$5, CAP.POS.P$6, CAP.POS.P$7, CAP.POS.P$8, CAP.POS.P$9, CAP.POS.P$10, U$8.PIN5 (5)
CAP_R: FCC_SIG_IN.P$3 (3); also elsewhere on the board
CAP_SENSOR: R5.1, U$8.PIN4 (4); also elsewhere on the board
CAP_VOLT: FCC_SIG_OUT.P$3 (3), R5.2, S1.2
CHARGE_R: FCC_SIG_IN.P$6 (6); also elsewhere on the board
CHARGING_RES_NEG: RES.NEG.P$1, RES.NEG.P$2, RES.NEG.P$3, RES.NEG.P$4, RES.NEG.P$5, RES.NEG.P$6, RES.NEG.P$7, RES.NEG.P$8, RES.NEG.P$9, RES.NEG.P$10; also elsewhere on the board
FC.12: FC-POWER-IN.1, FC-POWER-IN.3, U$15.P$2 (P(-)); also elsewhere on the board
FC_CURR: FCC_SIG_OUT.P$4 (4), U$7.PIN3 (3)
FC_POS: CAP.POS2.P$1, CAP.POS2.P$2, CAP.POS2.P$3, CAP.POS2.P$4, CAP.POS2.P$5, CAP.POS2.P$6, CAP.POS2.P$7, CAP.POS2.P$8, CAP.POS2.P$9, CAP.POS2.P$10, D1.(-), D1.C@1 ((-)), D1.C@2 ((-)), FC_POWER_BOARD_RELAY.7, FC_POWER_BOARD_RELAY.8, RES.POS.P$1, RES.POS.P$2, RES.POS.P$3, RES.POS.P$4, RES.POS.P$5, RES.POS.P$6, RES.POS.P$7, RES.POS.P$8, RES.POS.P$9, RES.POS.P$10, U$9.PIN4 (4); also elsewhere on the board
FC_POWER: CAP.POS1.P$1, CAP.POS1.P$2, CAP.POS1.P$3, CAP.POS1.P$4, CAP.POS1.P$5, CAP.POS1.P$6, CAP.POS1.P$7, CAP.POS1.P$8, CAP.POS1.P$9, CAP.POS1.P$10, D1.(+), U$7.PIN5 (5)
FC_POWER_OUT: FC-POWER-OUT.1, FC-POWER-OUT.3, FC-POWER-OUT.4, FC-POWER-OUT.6, FC_POWER_BOARD_RELAY.5, FC_POWER_BOARD_RELAY.6
FC_R: FCC_SIG_IN.P$2 (2), FC_POWER_BOARD_RELAY.LED+
FC_SENSOR: FC.POS.P$1, FC.POS.P$2, FC.POS.P$3, FC.POS.P$4, FC.POS.P$5, FC.POS.P$6, FC.POS.P$7, FC.POS.P$8, FC.POS.P$9, FC.POS.P$10, R6.1, U$7.PIN4 (4)
FC_VOLT: FCC_SIG_OUT.P$1 (1), R6.2, S2.2
GND: AUX-POWER-IN.2, AUX-POWER-IN.5, C1.2, C2.2, C3.2, CAP.GND.P$1, CAP.GND.P$2, CAP.GND.P$3, CAP.GND.P$4, CAP.GND.P$5, CAP.GND.P$6, CAP.GND.P$7, CAP.GND.P$8, CAP.GND.P$9, CAP.GND.P$10, FC-POWER-IN.2, FC-POWER-IN.5, FC-POWER-OUT.2, FC-POWER-OUT.5, FC.GND.P$1, FC.GND.P$2, FC.GND.P$3, FC.GND.P$4, FC.GND.P$5, FC.GND.P$6, FC.GND.P$7, FC.GND.P$8, FC.GND.P$9, FC.GND.P$10, FCC_SIG_OUT.P$8 (8), FC_POWER_BOARD_RELAY.LED-, MOTOR.GROUND.P$1, MOTOR.GROUND.P$2, MOTOR.GROUND.P$3, MOTOR.GROUND.P$4, MOTOR.GROUND.P$5, MOTOR.GROUND.P$6, MOTOR.GROUND.P$7, MOTOR.GROUND.P$8, MOTOR.GROUND.P$9, MOTOR.GROUND.P$10, R2.2, R4.2, R7.2, R14.2, R15.2, R16.2, U$7.PIN2 (2), U$8.PIN2 (2), U$9.PIN2 (2), U$15.P$1 (P(+)), U$16.P$1 (P(+)); also elsewhere on the board
ISO_GND: FCC_SIG_IN.P$7 (7), FCC_SIG_IN.P$8 (8), FCC_SIG_IN.P$13 (SHD1), FCC_SIG_IN.P$14 (SHD2), FCC_SIG_OUT.P$13 (SHD1), FCC_SIG_OUT.P$14 (SHD2); also elsewhere on the board
MOTOR_CURR: FCC_SIG_OUT.P$5 (5), U$9.PIN3 (3)
MOTOR_C_SENSOR: R8.1, U$9.PIN5 (5); also elsewhere on the board
MOTOR_POS: MOTOR.POSITIVE.P$1, MOTOR.POSITIVE.P$2, MOTOR.POSITIVE.P$3, MOTOR.POSITIVE.P$4, MOTOR.POSITIVE.P$5, MOTOR.POSITIVE.P$6, MOTOR.POSITIVE.P$7, MOTOR.POSITIVE.P$8, MOTOR.POSITIVE.P$9, MOTOR.POSITIVE.P$10; also elsewhere on the board
MOTOR_R: FCC_SIG_IN.P$4 (4); also elsewhere on the board
MOTOR_VOLT: FCC_SIG_OUT.P$2 (2), R8.2, S3.2
unnamed: R4.1, S1.1 (O)
unnamed: R14.1, S1.3 (S)
unnamed: R2.1, S3.1 (O)
unnamed: R15.1, S3.3 (S)
unnamed: R7.1, S2.1 (O)
unnamed: R16.1, S2.3 (S)
NC: FCC_SIG_IN.P$1 (1), FCC_SIG_OUT.P$7 (7)
START_R: FCC_SIG_IN.P$5 (5); also elsewhere on the board

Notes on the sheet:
FC Current Sensor
Charging Resistor Positive
Charging Resistor Negative
Motor Current Sensor
FC (+)
FC (-)
Voltage Sensors
Power Blocks and Diodes
Signals
DIODE BYPASS (+)
DIODE BYPASS (-)
Current Sensors
Capacitor Current Sensor
CAP Pos
CAP GND
MOTOR GND
MOTOR POS
Low Power Relay
Power

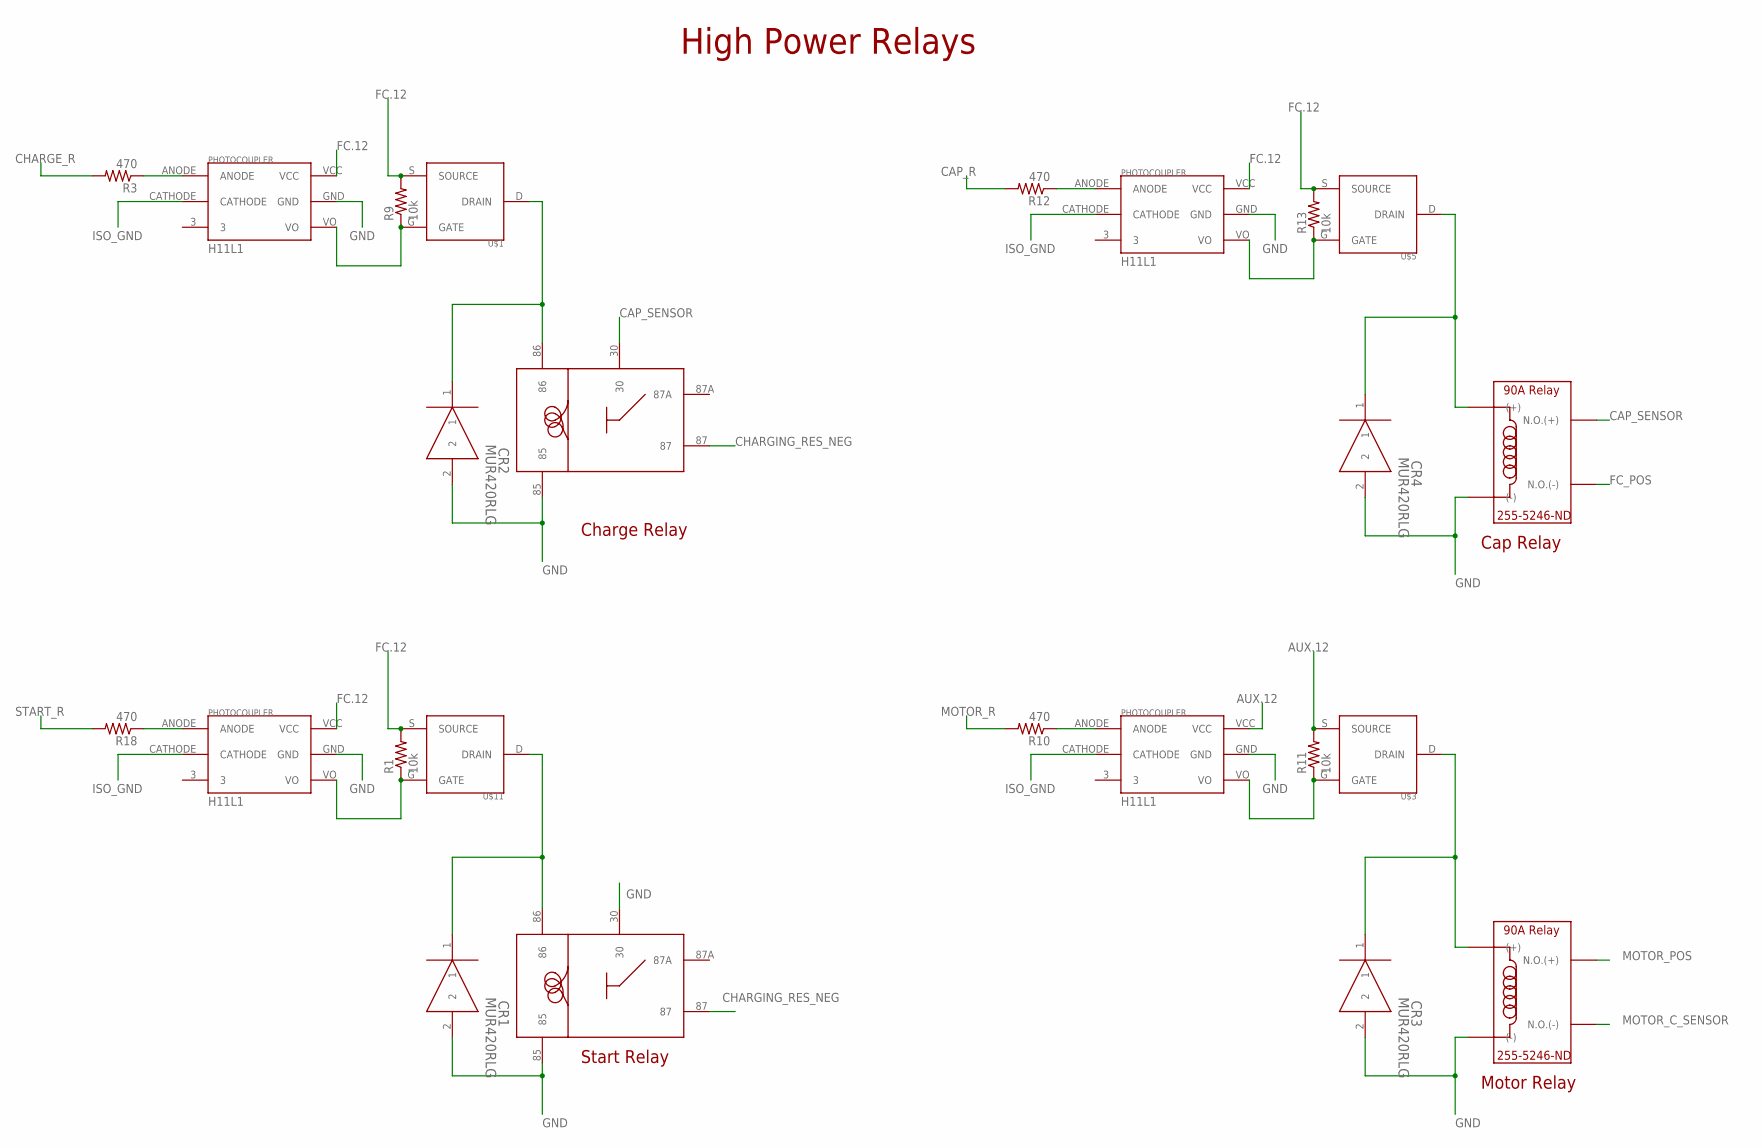
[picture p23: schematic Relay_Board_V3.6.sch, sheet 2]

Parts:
CR1, CR2, CR3, CR4: MUR420RLG; DO-201AD
R1, R9, R11, R13: 10k; 0603-RES
R3, R10, R12, R18: 470; 0603-RES
START.RELAY1, START.RELAY2: VCF4-1000
U$1, U$3, U$5, U$11: DMP3056L-7DMP3056L-7; DMP3056L-7
U$2, U$4, U$6, U$12: H11L1H11L1; H11L1
U$13, U$14: 255-5246-ND

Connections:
AUX.12: R11.2, U$3.S (SOURCE), U$4.VCC; also elsewhere on the board
CAP_R: R12.2; also elsewhere on the board
CAP_SENSOR: START.RELAY2.30, U$13.NO(+) (N.O.(+)), U$13.NO(++) (N.O.(+)); also elsewhere on the board
CHARGE_R: R3.2; also elsewhere on the board
CHARGING_RES_NEG: START.RELAY1.87, START.RELAY2.87; also elsewhere on the board
FC.12: R1.2, R9.2, R13.2, U$1.S (SOURCE), U$2.VCC, U$5.S (SOURCE), U$6.VCC, U$11.S (SOURCE), U$12.VCC; also elsewhere on the board
FC_POS: U$13.NO(-) (N.O.(-)), U$13.NO(--) (N.O.(-)); also elsewhere on the board
GND: CR1.2, CR2.2, CR3.2, CR4.2, START.RELAY1.30, START.RELAY1.85, START.RELAY2.85, U$2.GND, U$4.GND, U$6.GND, U$12.GND, U$13.(-), U$13.(--) ((-)), U$14.(-), U$14.(--) ((-)); also elsewhere on the board
ISO_GND: U$2.CATHODE, U$4.CATHODE, U$6.CATHODE, U$12.CATHODE; also elsewhere on the board
MOTOR_C_SENSOR: U$14.NO(-) (N.O.(-)), U$14.NO(--) (N.O.(-)); also elsewhere on the board
MOTOR_POS: U$14.NO(+) (N.O.(+)), U$14.NO(++) (N.O.(+)); also elsewhere on the board
MOTOR_R: R10.2; also elsewhere on the board
unnamed: R9.1, U$1.G (GATE), U$2.VO
unnamed: R3.1, U$2.ANODE
unnamed: CR2.1, START.RELAY2.86, U$1.D (DRAIN)
unnamed: R11.1, U$3.G (GATE), U$4.VO
unnamed: R10.1, U$4.ANODE
unnamed: CR3.1, U$3.D (DRAIN), U$14.(+), U$14.(++) ((+))
unnamed: R13.1, U$5.G (GATE), U$6.VO
unnamed: R12.1, U$6.ANODE
unnamed: CR4.1, U$5.D (DRAIN), U$13.(+), U$13.(++) ((+))
unnamed: R1.1, U$11.G (GATE), U$12.VO
unnamed: R18.1, U$12.ANODE
unnamed: CR1.1, START.RELAY1.86, U$11.D (DRAIN)
START_R: R18.2; also elsewhere on the board

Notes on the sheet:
Start Relay
Charge Relay
High Power Relays
Motor Relay
Cap Relay

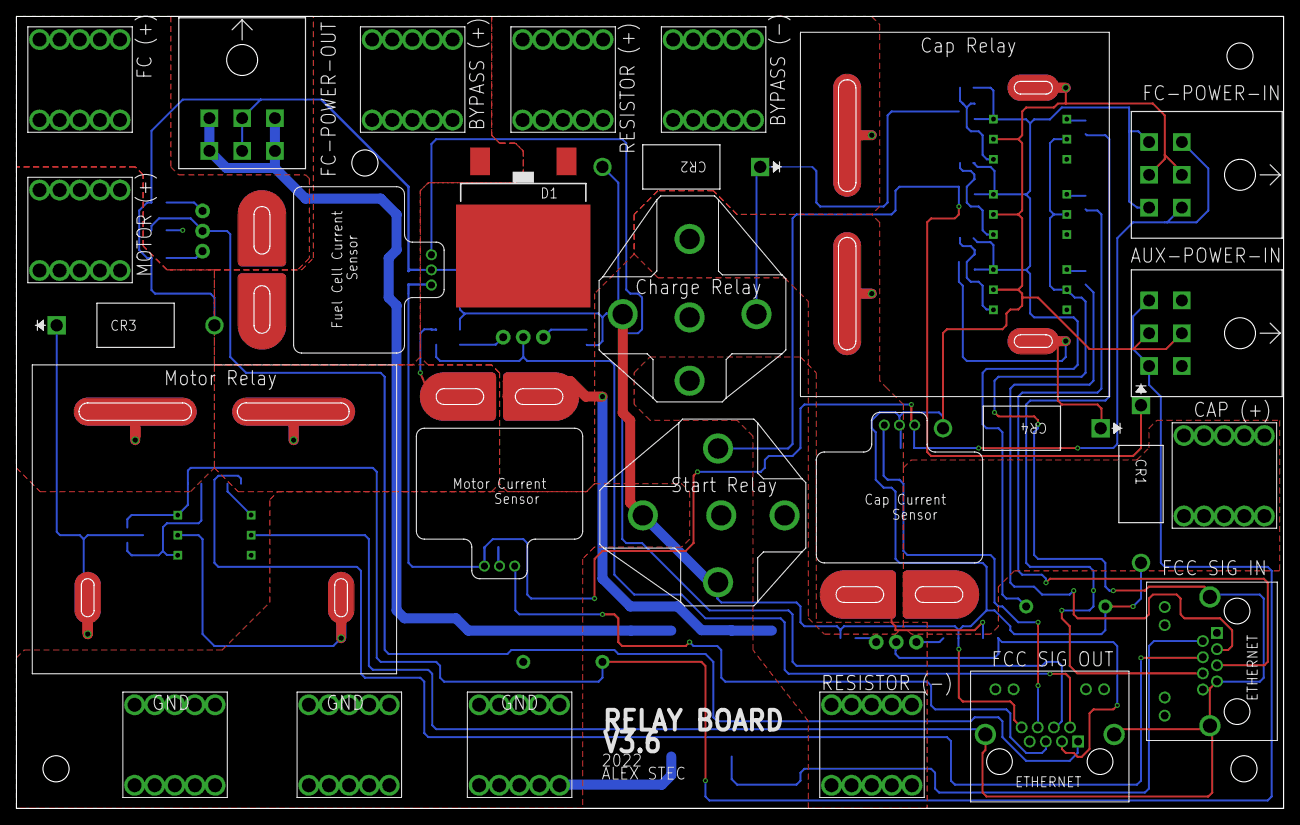
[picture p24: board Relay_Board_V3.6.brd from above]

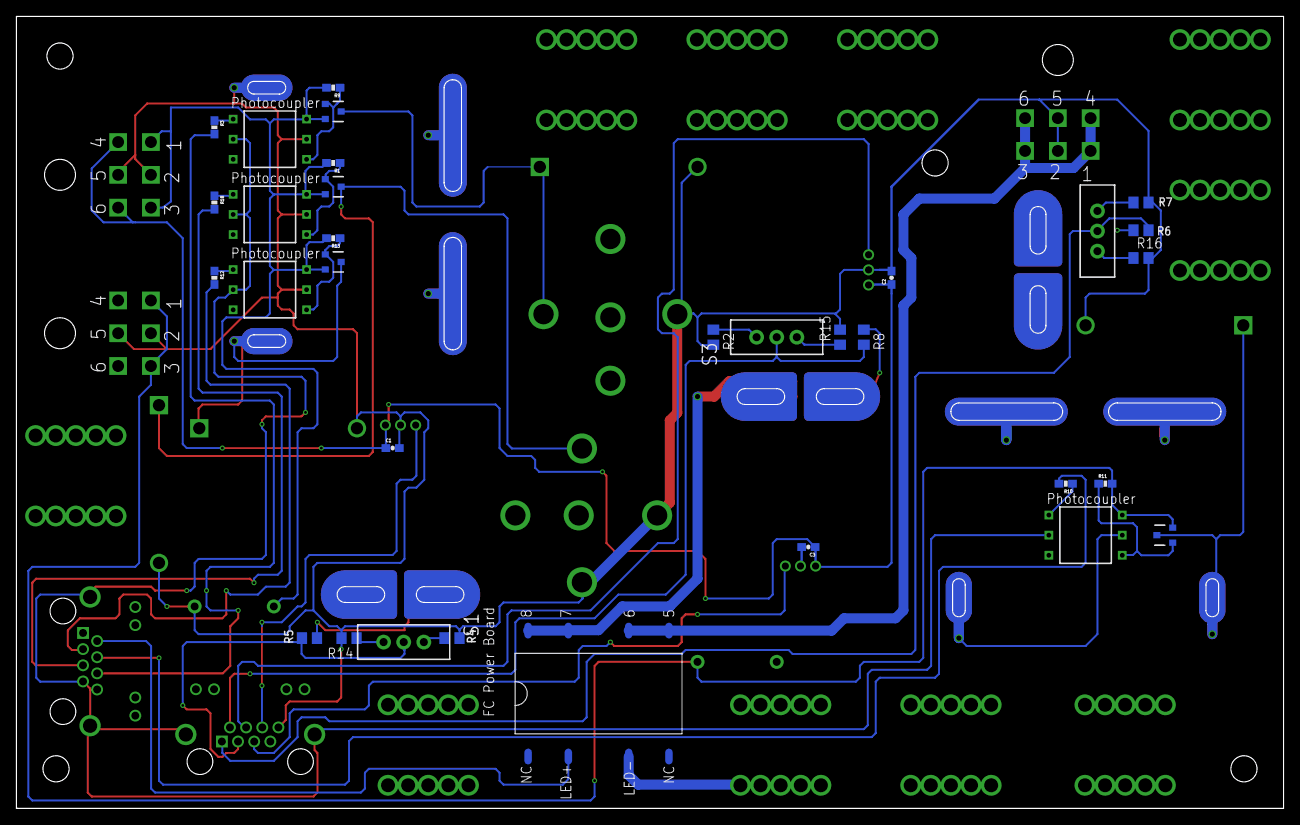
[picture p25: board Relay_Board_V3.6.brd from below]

Board: 2 copper layers, 160.0 x 100.0 mm, 65 parts (32 on the bottom side), 44 nets.

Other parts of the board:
U$18, U$20, U$21, U$23: STAND-OFF

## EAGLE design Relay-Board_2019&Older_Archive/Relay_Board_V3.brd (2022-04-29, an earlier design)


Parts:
C1, C2, C3: CAP0603-CAP; 0603-CAP
CAP.GND, CAP.GND1, CAP.POS1, CAP.POS2: 732-3204-ND_CONNECTOR; 732-3204-ND
FC.GND, FC.POS: 732-3204-ND_CONNECTOR; 732-3204-ND
FCC_1, FCC_2: ETHERNET; A122645-ND
MOTOR.GROUND, MOTOR.POSITIVE: 732-3204-ND_CONNECTOR; 732-3204-ND
R2, R4: 750(<1%); R0805
R5, R8: 9250 (<1%); R0805
R6: 9250(1%); R0805
R7: 750(1%); R0805
RES.NEG, RES.POS: 732-3204-ND_CONNECTOR; 732-3204-ND
U$7, U$8, U$9: ACS770LCB_CURRENTSENSOR
U$19: 5555140-6; 1734723-1_RJ11
U$22: RELAY-CPC1907B

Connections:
5V: C1.1, C2.1, C3.1, FCC_1.P$1 (1), FCC_2.P$7 (7), U$7.PIN1 (1), U$8.PIN1 (1), U$9.PIN1 (1)
CAP_CURR: FCC_2.P$5 (5), U$8.PIN3 (3)
CAP_FUSE: CAP.GND1.P$1, CAP.GND1.P$2, CAP.GND1.P$3, CAP.GND1.P$4, CAP.GND1.P$5, CAP.GND1.P$6, CAP.GND1.P$7, CAP.GND1.P$8, CAP.GND1.P$9, CAP.GND1.P$10, U$8.PIN5 (5); also elsewhere on the board
CAP_R: FCC_1.P$3 (3); also elsewhere on the board
CAP_SENSOR: R5.1, U$8.PIN4 (4)
CAP_VOLT: FCC_2.P$2 (2), R4.2, R5.2
CHARGE_R: FCC_1.P$6 (6); also elsewhere on the board
CHARGING_RES_NEG: RES.NEG.P$1, RES.NEG.P$2, RES.NEG.P$3, RES.NEG.P$4, RES.NEG.P$5, RES.NEG.P$6, RES.NEG.P$7, RES.NEG.P$8, RES.NEG.P$9, RES.NEG.P$10; also elsewhere on the board
FCC_R: FCC_1.P$2 (2), U$22.LED+
FC_CURR: FCC_2.P$4 (4), U$7.PIN3 (3)
FC_POS: CAP.POS2.P$1, CAP.POS2.P$2, CAP.POS2.P$3, CAP.POS2.P$4, CAP.POS2.P$5, CAP.POS2.P$6, CAP.POS2.P$7, CAP.POS2.P$8, CAP.POS2.P$9, CAP.POS2.P$10, RES.POS.P$1, RES.POS.P$2, RES.POS.P$3, RES.POS.P$4, RES.POS.P$5, RES.POS.P$6, RES.POS.P$7, RES.POS.P$8, RES.POS.P$9, RES.POS.P$10, U$9.PIN4 (4), U$22.7, U$22.8; also elsewhere on the board
FC_POWER: CAP.POS1.P$1, CAP.POS1.P$2, CAP.POS1.P$3, CAP.POS1.P$4, CAP.POS1.P$5, CAP.POS1.P$6, CAP.POS1.P$7, CAP.POS1.P$8, CAP.POS1.P$9, CAP.POS1.P$10, U$7.PIN5 (5)
FC_SENSOR: R6.1, U$7.PIN4 (4)
FC_VOLT: FCC_2.P$1 (1), R6.2, R7.2
GND: C1.2, C2.2, C3.2, CAP.GND.P$1, CAP.GND.P$2, CAP.GND.P$3, CAP.GND.P$4, CAP.GND.P$5, CAP.GND.P$6, CAP.GND.P$7, CAP.GND.P$8, CAP.GND.P$9, CAP.GND.P$10, FC.GND.P$1, FC.GND.P$2, FC.GND.P$3, FC.GND.P$4, FC.GND.P$5, FC.GND.P$6, FC.GND.P$7, FC.GND.P$8, FC.GND.P$9, FC.GND.P$10, FCC_2.P$8 (8), MOTOR.GROUND.P$1, MOTOR.GROUND.P$2, MOTOR.GROUND.P$3, MOTOR.GROUND.P$4, MOTOR.GROUND.P$5, MOTOR.GROUND.P$6, MOTOR.GROUND.P$7, MOTOR.GROUND.P$8, MOTOR.GROUND.P$9, MOTOR.GROUND.P$10, R2.1, R4.1, R7.1, U$7.PIN2 (2), U$8.PIN2 (2), U$9.PIN2 (2), U$19.1, U$19.6, U$19.SH1, U$19.SH2, U$22.LED-; also elsewhere on the board
ISO_GND: FCC_1.P$7 (7), FCC_1.P$8 (8), FCC_1.P$13 (SHD1), FCC_1.P$14 (SHD2), FCC_2.P$13 (SHD1), FCC_2.P$14 (SHD2); also elsewhere on the board
MOTOR_CURR: FCC_2.P$6 (6), U$9.PIN3 (3)
MOTOR_C_SENSOR: R8.1, U$9.PIN5 (5); also elsewhere on the board
MOTOR_POS: MOTOR.POSITIVE.P$1, MOTOR.POSITIVE.P$2, MOTOR.POSITIVE.P$3, MOTOR.POSITIVE.P$4, MOTOR.POSITIVE.P$5, MOTOR.POSITIVE.P$6, MOTOR.POSITIVE.P$7, MOTOR.POSITIVE.P$8, MOTOR.POSITIVE.P$9, MOTOR.POSITIVE.P$10; also elsewhere on the board
MOTOR_R: FCC_1.P$4 (4); also elsewhere on the board
MOTOR_VOLT: FCC_2.P$3 (3), R2.2, R8.2
POWER_BOARD: U$19.2, U$19.3, U$19.4, U$19.5, U$22.5, U$22.6
POWER_IN: FC.POS.P$1, FC.POS.P$2, FC.POS.P$3, FC.POS.P$4, FC.POS.P$5, FC.POS.P$6, FC.POS.P$7, FC.POS.P$8, FC.POS.P$9, FC.POS.P$10
START_R: FCC_1.P$5 (5); also elsewhere on the board

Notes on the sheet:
FC Current Sensor
Charging Resistor Positive
Charging Resistor Negative
Motor Current Sensor
FC (+)
FC (-)
Voltage Sensors
Power Blocks and Diodes
Signals
DIODE BYPASS (+)
DIODE BYPASS (-)
Current Sensors
Capacitor Current Sensor
CAP Pos
CAP GND
MOTOR GND
MOTOR POS
Low Power Relay
(INSERT DIODE HERE)


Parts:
CR1, CR2, CR3, CR4: MUR420RLG; DO-201AD
R1, R9, R11, R13: 10k; 0603-RES
R3, R10, R12, R18: 470; 0603-RES
START.RELAY1, START.RELAY2, START.RELAY3, START.RELAY4: VCF4-1000
U$1, U$3, U$5, U$11: DMP3056L-7DMP3056L-7; DMP3056L-7
U$2, U$4, U$6, U$12: H11L1H11L1; H11L1

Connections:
AUX.12: R11.2, U$3.S (SOURCE), U$4.VCC
CAP_FUSE: START.RELAY2.30, START.RELAY4.30; also elsewhere on the board
CAP_R: R12.2; also elsewhere on the board
CHARGE_R: R3.2; also elsewhere on the board
CHARGING_RES_NEG: START.RELAY1.87, START.RELAY2.87; also elsewhere on the board
FC.12: R1.2, R9.2, R13.2, U$1.S (SOURCE), U$2.VCC, U$5.S (SOURCE), U$6.VCC, U$11.S (SOURCE), U$12.VCC
FC_POS: START.RELAY4.87; also elsewhere on the board
GND: CR1.2, CR2.2, CR3.2, CR4.2, START.RELAY1.30, START.RELAY1.85, START.RELAY2.85, START.RELAY3.85, START.RELAY4.85, U$2.GND, U$4.GND, U$6.GND, U$12.GND; also elsewhere on the board
ISO_GND: U$2.CATHODE, U$4.CATHODE, U$6.CATHODE, U$12.CATHODE; also elsewhere on the board
MOTOR_C_SENSOR: START.RELAY3.87; also elsewhere on the board
MOTOR_POS: START.RELAY3.30; also elsewhere on the board
MOTOR_R: R10.2; also elsewhere on the board
unnamed: R9.1, U$1.G (GATE), U$2.VO
unnamed: R3.1, U$2.ANODE
unnamed: CR2.1, START.RELAY2.86, U$1.D (DRAIN)
unnamed: R11.1, U$3.G (GATE), U$4.VO
unnamed: R10.1, U$4.ANODE
unnamed: CR3.1, START.RELAY3.86, U$3.D (DRAIN)
unnamed: R13.1, U$5.G (GATE), U$6.VO
unnamed: R12.1, U$6.ANODE
unnamed: CR4.1, START.RELAY4.86, U$5.D (DRAIN)
unnamed: R1.1, U$11.G (GATE), U$12.VO
unnamed: R18.1, U$12.ANODE
unnamed: CR1.1, START.RELAY1.86, U$11.D (DRAIN)
START_R: R18.2; also elsewhere on the board

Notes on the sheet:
Start Relay
Charge Relay
High Power Relays
Motor Relay
Cap Relay


Board: 2 copper layers, 179.0 x 762.0 mm, 51 parts (0 on the bottom side), 38 nets.

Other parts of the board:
U$16: LOGO

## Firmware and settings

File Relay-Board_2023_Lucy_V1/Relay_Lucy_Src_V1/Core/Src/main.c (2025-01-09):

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
/* Includes ------------------------------------------------------------------*/
#include "main.h"
#include "cmsis_os.h"
#include "cmsis_os2.h"
#include "stm32f4xx_hal_def.h"
#include "usb_device.h"

/* USER CODE BEGIN Includes */
#include "canid.h"
#include "usbd_cdc_if.h"
#include <stdint.h>
/* USER CODE END Includes */

typedef StaticTask_t osStaticThreadDef_t;
typedef StaticQueue_t osStaticMessageQDef_t;
/* USER CODE BEGIN PTD */
typedef enum {
  ALL_RELAY_OFF = 0x00,
  CAP_RELAY = 0x01,
  RES_RELAY = 0x02,
  DSCHRGE_RELAY = 0x04,
  MTR_RELAY = 0x08,
} relayBit_t;

typedef enum {
  RELAY_STBY = ALL_RELAY_OFF,
  RELAY_STRTP = RES_RELAY | DSCHRGE_RELAY,
  RELAY_CHRGE = RES_RELAY,
  RELAY_RUN = CAP_RELAY | DSCHRGE_RELAY | MTR_RELAY,
} rbState_t;

typedef struct {
  float fc_volt;
  float fc_curr;
  float mtr_volt;
  float mtr_curr;
  float cap_volt;
  float cap_curr;
} rbData_t;

typedef struct {
  uint8_t H2_OK;
} canData_t;

/* USER CODE END PTD */

/* USER CODE BEGIN PD */
#define CAN_MESSAGE_SENT_TIMEOUT_MS 500
#define CAN_ADD_TX_TIMEOUT_MS 500

#define FULL_CAP_CHARGE_V 20

#define CAN_TX_MAILBOX_NONE 0x00000000U // Remove reference to tx mailbox
/* USER CODE END PD */

ADC_HandleTypeDef hadc1;
ADC_HandleTypeDef hadc2;
DMA_HandleTypeDef hdma_adc1;
DMA_HandleTypeDef hdma_adc2;

CAN_HandleTypeDef hcan1;

/* Definitions for RelayTask */
osThreadId_t RelayTaskHandle;
uint32_t RelayTaskBuffer[256];
osStaticThreadDef_t RelayTaskControlBlock;
const osThreadAttr_t RelayTask_attributes = {
    .name = "RelayTask",
    .cb_mem = &RelayTaskControlBlock,
    .cb_size = sizeof(RelayTaskControlBlock),
    .stack_mem = &RelayTaskBuffer[0],
    .stack_size = sizeof(RelayTaskBuffer),
    .priority = (osPriority_t)osPriorityNormal,
};
/* Definitions for CanRtrTask */
osThreadId_t CanRtrTaskHandle;
uint32_t CanRtrTaskBuffer[256];
osStaticThreadDef_t CanRtrTaskControlBlock;
const osThreadAttr_t CanRtrTask_attributes = {
    .name = "CanRtrTask",
    .cb_mem = &CanRtrTaskControlBlock,
    .cb_size = sizeof(CanRtrTaskControlBlock),
    .stack_mem = &CanRtrTaskBuffer[0],
    .stack_size = sizeof(CanRtrTaskBuffer),
    .priority = (osPriority_t)osPriorityNormal,
};
/* Definitions for AdcTask */
osThreadId_t AdcTaskHandle;
uint32_t AdcTaskBuffer[256];
osStaticThreadDef_t AdcTaskControlBlock;
const osThreadAttr_t AdcTask_attributes = {
    .name = "AdcTask",
    .cb_mem = &AdcTaskControlBlock,
    .cb_size = sizeof(AdcTaskControlBlock),
    .stack_mem = &AdcTaskBuffer[0],
    .stack_size = sizeof(AdcTaskBuffer),
    .priority = (osPriority_t)osPriorityNormal,
};
/* Definitions for IndicateLedTask */
osThreadId_t IndicateLedTaskHandle;
uint32_t IndicateLedTaskBuffer[256];
osStaticThreadDef_t IndicateLedTaskControlBlock;
const osThreadAttr_t IndicateLedTask_attributes = {
    .name = "IndicateLedTask",
    .cb_mem = &IndicateLedTaskControlBlock,
    .cb_size = sizeof(IndicateLedTaskControlBlock),
    .stack_mem = &IndicateLedTaskBuffer[0],
    .stack_size = sizeof(IndicateLedTaskBuffer),
    .priority = (osPriority_t)osPriorityNormal4,
};
/* Definitions for CanDataTask */
osThreadId_t CanDataTaskHandle;
uint32_t CanDataTaskBuffer[256];
osStaticThreadDef_t CanDataTaskControlBlock;
const osThreadAttr_t CanDataTask_attributes = {
    .name = "CanDataTask",
    .cb_mem = &CanDataTaskControlBlock,
    .cb_size = sizeof(CanDataTaskControlBlock),
    .stack_mem = &CanDataTaskBuffer[0],
    .stack_size = sizeof(CanDataTaskBuffer),
    .priority = (osPriority_t)osPriorityNormal4,
};
/* Definitions for canRxRtrMsgQueue */
osMessageQueueId_t canRxRtrMsgQueueHandle;
uint8_t canRxRtrMsgQueueBuffer[128 * sizeof(uint32_t)];
osStaticMessageQDef_t canRxRtrMsgQueueControlBlock;
const osMessageQueueAttr_t canRxRtrMsgQueue_attributes = {
    .name = "canRxRtrMsgQueue",
    .cb_mem = &canRxRtrMsgQueueControlBlock,
    .cb_size = sizeof(canRxRtrMsgQueueControlBlock),
    .mq_mem = &canRxRtrMsgQueueBuffer,
    .mq_size = sizeof(canRxRtrMsgQueueBuffer)};
/* Definitions for canRxDataMsgQueue */
osMessageQueueId_t canRxDataMsgQueueHandle;
uint8_t canRxDataMsgQueueBuffer[16 * sizeof(uint16_t)];
osStaticMessageQDef_t canRxDataMsgQueueControlBlock;
const osMessageQueueAttr_t canRxDataMsgQueue_attributes = {
    .name = "canRxDataMsgQueue",
    .cb_mem = &canRxDataMsgQueueControlBlock,
    .cb_size = sizeof(canRxDataMsgQueueControlBlock),
    .mq_mem = &canRxDataMsgQueueBuffer,
    .mq_size = sizeof(canRxDataMsgQueueBuffer)};
/* Definitions for canMsgReceivedSem */
osSemaphoreId_t canMsgReceivedSemHandle;
const osSemaphoreAttr_t canMsgReceivedSem_attributes = {
    .name = "canMsgReceivedSem"};
/* USER CODE BEGIN PV */
rbState_t rb_state = RELAY_STBY;
rbData_t relay_board_data;

volatile uint16_t adc1Results[3];
volatile uint16_t adc2Results[3];

CAN_RxHeaderTypeDef RxHeader;
uint8_t RxData[8];
uint32_t TxMailboxCanTask;
/* USER CODE END PV */

void SystemClock_Config(void);
static void MX_GPIO_Init(void);
static void MX_DMA_Init(void);
static void MX_CAN1_Init(void);
static void MX_ADC1_Init(void);
static void MX_ADC2_Init(void);
void StartRelayTask(void *argument);
void StartCanRtrTask(void *argument);
void StartAdcTask(void *argument);
void StartIndicateLedTask(void *argument);
void StartCanDataTask(void *argument);

/* USER CODE BEGIN PFP */
int _write(int file, char *ptr, int len) {
  CDC_Transmit_FS((uint8_t *)ptr, (uint16_t)len);
  return len;
}

/**
 * The canRxMsqQueue is 32 items each slot with 4 bytes
 * in it. The StdID is a uint32_t according to HAL and the
 * RxData is 8 items of 1 byte each. Thus osMessageQueuePut
 * will add 4 items from RxData when you pass the pointer
 * to it.
 */
void HAL_CAN_RxFifo0MsgPendingCallback(CAN_HandleTypeDef *hcan) {
  HAL_CAN_GetRxMessage(hcan, CAN_RX_FIFO0, &RxHeader, RxData);
  if (RxHeader.RTR == CAN_RTR_REMOTE) {
    osMessageQueuePut(canRxRtrMsgQueueHandle, &RxHeader.StdId, 0U, 0UL);
  } else {
    osMessageQueuePut(canRxDataMsgQueueHandle, &RxHeader.StdId, 0U, 0UL);
    if (RxHeader.DLC <= 4UL) {
      osMessageQueuePut(canRxDataMsgQueueHandle, RxData, 0U, 0UL);
    } else {
      osMessageQueuePut(canRxDataMsgQueueHandle, RxData, 0U, 0UL);
      osMessageQueuePut(canRxDataMsgQueueHandle, &RxData[4], 0U, 0UL);
    }
  }
}

// void HAL_CAN_RxFifo1MsgPendingCallback(CAN_HandleTypeDef *hcan) {
//   HAL_CAN_GetRxMessage(hcan, CAN_RX_FIFO1, &RxHeader, RxData);
//   osMessageQueuePut(canRxMsgQueueHandle, &RxHeader.StdId, 0U, 0UL);
//   // need condition for either 4 byte or 8 byte
//   if (RxHeader.DLC == 0UL) {
//     // Data request, don't add anything else to queue
//   } else if (RxHeader.DLC <= 4UL) {
//     osMessageQueuePut(canRxMsgQueueHandle, RxData, 0U, 0UL);
//   } else {
//     osMessageQueuePut(canRxMsgQueueHandle, RxData, 0U, 0UL);
//     osMessageQueuePut(canRxMsgQueueHandle, RxData + 4, 0U, 0UL);
//   }
// }

/* Transmit Completed Callbacks for Message Sent Confirmations */
void HAL_CAN_TxMailbox0CompleteCallback(CAN_HandleTypeDef *hcan) {
  if (TxMailboxCanTask == CAN_TX_MAILBOX0) {
    osSemaphoreRelease(canMsgReceivedSemHandle);
    TxMailboxCanTask = CAN_TX_MAILBOX_NONE;
  }
}
void HAL_CAN_TxMailbox1CompleteCallback(CAN_HandleTypeDef *hcan) {
  if (TxMailboxCanTask == CAN_TX_MAILBOX1) {
    osSemaphoreRelease(canMsgReceivedSemHandle);
    TxMailboxCanTask = CAN_TX_MAILBOX_NONE;
  }
}
void HAL_CAN_TxMailbox2CompleteCallback(CAN_HandleTypeDef *hcan) {
  if (TxMailboxCanTask == CAN_TX_MAILBOX2) {
    osSemaphoreRelease(canMsgReceivedSemHandle);
    TxMailboxCanTask = CAN_TX_MAILBOX_NONE;
  }
}

// Counter for both DMA conversions to be Completed
// Utilized in ADC Thread below
uint32_t conversion_completed = 0;

void HAL_ADC_ConvCpltCallback(ADC_HandleTypeDef *hadc) {
  if (hadc->Instance == hadc1.Instance) {
    conversion_completed++;
  }
  if (hadc->Instance == hadc2.Instance) {
    conversion_completed++;
  }
}

HAL_StatusTypeDef HAL_CAN_SafeAddTxMessage(uint8_t *msg, uint32_t msg_id,
                                           uint32_t msg_length,
                                           uint32_t *TxMailbox, uint32_t rtr) {
  uint32_t fc_tick;
  HAL_StatusTypeDef hal_stat;
  CAN_TxHeaderTypeDef TxHeader;

  // These will never change
  TxHeader.IDE = CAN_ID_STD;
  TxHeader.ExtId = 0;
  TxHeader.TransmitGlobalTime = DISABLE;

  // User will give us this information
  TxHeader.RTR = rtr;
  TxHeader.StdId = msg_id;
  TxHeader.DLC = msg_length;

  // Start a timer to check timeout conditions
  fc_tick = HAL_GetTick();
 
  /* Try to add a Tx message. Returns HAL_ERROR if there are no avail
   * mailboxes or if the peripheral is not initialized. */
  do {
    hal_stat = HAL_CAN_AddTxMessage(&hcan1, &TxHeader, msg, TxMailbox);
  } while (hal_stat != HAL_OK &&
           ((HAL_GetTick() - fc_tick) < CAN_ADD_TX_TIMEOUT_MS));

  return hal_stat;
}
/* USER CODE END PFP */

/**
 * @brief  The application entry point.
 * @retval int
 */
int main(void) {
  /* MCU Configuration--------------------------------------------------------*/

  /* Reset of all peripherals, Initializes the Flash interface and the Systick.
   */
  HAL_Init();

  /* Configure the system clock */
  SystemClock_Config();

  /* Initialize all configured peripherals */
  MX_GPIO_Init();
  MX_DMA_Init();
  MX_CAN1_Init();
  MX_ADC1_Init();
  MX_ADC2_Init();
  /* Init scheduler */
  osKernelInitialize();

  /* USER CODE BEGIN RTOS_MUTEX */
  /* add mutexes, ... */
  /* USER CODE END RTOS_MUTEX */

  /* Create the semaphores(s) */
  /* creation of canMsgReceivedSem */
  canMsgReceivedSemHandle = osSemaphoreNew(1, 0, &canMsgReceivedSem_attributes);

  /* USER CODE BEGIN RTOS_SEMAPHORES */
  /* add semaphores, ... */
  /* USER CODE END RTOS_SEMAPHORES */

  /* USER CODE BEGIN RTOS_TIMERS */
  /* start timers, add new ones, ... */
  /* USER CODE END RTOS_TIMERS */

  /* Create the queue(s) */
  /* creation of canRxRtrMsgQueue */
  canRxRtrMsgQueueHandle =
      osMessageQueueNew(128, sizeof(uint32_t), &canRxRtrMsgQueue_attributes);

  /* creation of canRxDataMsgQueue */
  canRxDataMsgQueueHandle =
      osMessageQueueNew(16, sizeof(uint16_t), &canRxDataMsgQueue_attributes);

  /* USER CODE BEGIN RTOS_QUEUES */
  /* add queues, ... */
  /* USER CODE END RTOS_QUEUES */

  /* Create the thread(s) */
  /* creation of RelayTask */
  RelayTaskHandle = osThreadNew(StartRelayTask, NULL, &RelayTask_attributes);

  /* creation of CanRtrTask */
  CanRtrTaskHandle = osThreadNew(StartCanRtrTask, NULL, &CanRtrTask_attributes);

  /* creation of AdcTask */
  AdcTaskHandle = osThreadNew(StartAdcTask, NULL, &AdcTask_attributes);

  /* creation of IndicateLedTask */
  IndicateLedTaskHandle =
     osThreadNew(StartIndicateLedTask, NULL, &IndicateLedTask_attributes);

  /* creation of CanDataTask */
  CanDataTaskHandle =
      osThreadNew(StartCanDataTask, NULL, &CanDataTask_attributes);

  /* USER CODE BEGIN RTOS_THREADS */
  /* add threads, ... */
  /* USER CODE END RTOS_THREADS */

  /* USER CODE BEGIN RTOS_EVENTS */
  /* add events, ... */
  /* USER CODE END RTOS_EVENTS */

  /* Start scheduler */
  osKernelStart();

  /* We should never get here as control is now taken by the scheduler */
  /* Infinite loop */
  /* USER CODE BEGIN WHILE */

  while (1) {
    /* USER CODE END WHILE */

    /* USER CODE BEGIN 3 */
  }
  /* USER CODE END 3 */
}

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
/* USER CODE BEGIN Header_StartRelayTask */
/**
 * @brief  Function implementing the RelayTask thread.
 * @param  argument: Not used
 * @retval None
 */
/* USER CODE END Header_StartRelayTask */
void StartRelayTask(void *argument) {
  /* init code for USB_DEVICE */
  MX_USB_DEVICE_Init();
  /* USER CODE BEGIN 5 */
  HAL_CAN_ActivateNotification(&hcan1, CAN_IT_RX_FIFO0_MSG_PENDING);
  HAL_CAN_ActivateNotification(&hcan1, CAN_IT_RX_FIFO1_MSG_PENDING);
  HAL_CAN_ActivateNotification(&hcan1, CAN_IT_TX_MAILBOX_EMPTY);
  /* Infinite loop */
  rb_state = RELAY_STBY;
  for (;;) {
    switch (rb_state) {
    case RELAY_STBY:
      HAL_GPIO_WritePin(GPIOB,
                        DSCHRGE_RELAY_Pin | RES_RELAY_Pin | CAP_RELAY_Pin |
                            MTR_RELAY_Pin | DSCHRGE_LED_Pin | RES_LED_Pin |
                            MTR_LED_Pin | CAP_LED_Pin,
                        GPIO_PIN_RESET);
      break;
    case RELAY_STRTP:
      HAL_GPIO_WritePin(
          GPIOB, CAP_RELAY_Pin | MTR_RELAY_Pin | MTR_LED_Pin | CAP_LED_Pin,
          GPIO_PIN_RESET);
      HAL_GPIO_WritePin(GPIOB,
                        DSCHRGE_RELAY_Pin | RES_RELAY_Pin | DSCHRGE_LED_Pin |
                            RES_LED_Pin,
                        GPIO_PIN_SET);
      break;
    case RELAY_CHRGE:
      HAL_GPIO_WritePin(GPIOB,
                        DSCHRGE_RELAY_Pin | CAP_RELAY_Pin | MTR_RELAY_Pin |
                            DSCHRGE_LED_Pin | MTR_LED_Pin | CAP_LED_Pin,
                        GPIO_PIN_RESET);
      HAL_GPIO_WritePin(GPIOB, RES_RELAY_Pin | RES_LED_Pin, GPIO_PIN_SET);
      break;
    case RELAY_RUN:
      HAL_GPIO_WritePin(GPIOB, RES_RELAY_Pin | RES_LED_Pin, GPIO_PIN_RESET);
      HAL_GPIO_WritePin(GPIOB,
                        DSCHRGE_RELAY_Pin | CAP_RELAY_Pin | MTR_RELAY_Pin |
                            DSCHRGE_LED_Pin | MTR_LED_Pin | CAP_LED_Pin,
                        GPIO_PIN_SET);
      break;
    }
    osDelay(10);
  }
  /* USER CODE END 5 */
}

/* USER CODE BEGIN Header_StartCanRtrTask */
/**
 * @brief Function implementing the CanRtrTask thread.
 * @param argument: Not used
 * @retval None
 */
/* USER CODE END Header_StartCanRtrTask */
void StartCanRtrTask(void *argument) {
  /* USER CODE BEGIN StartCanRtrTask */
  float floatPackage[2] = {0.0F};
  uint32_t queueData = 0;
  HAL_StatusTypeDef hal_stat;
  /* Infinite loop */
  for (;;) {
    if (osMessageQueueGet(canRxRtrMsgQueueHandle, &queueData, 0U,
                          osWaitForever) == osOK) {
      switch (queueData) {
      case FUEL_CELL_PACKET:
        floatPackage[0] = relay_board_data.fc_volt;
        floatPackage[1] = relay_board_data.fc_curr;
        hal_stat =
            HAL_CAN_SafeAddTxMessage((uint8_t *)&floatPackage, FUEL_CELL_PACKET,
                                     8UL, &TxMailboxCanTask, CAN_RTR_DATA);
        break;
      case MOTOR_PACKET:
        floatPackage[0] = relay_board_data.mtr_volt;
        floatPackage[1] = relay_board_data.mtr_curr;
        hal_stat =
            HAL_CAN_SafeAddTxMessage((uint8_t *)&floatPackage, MOTOR_PACKET,
                                     8UL, &TxMailboxCanTask, CAN_RTR_DATA);
        break;
      case CAPACITOR_PACKET:
        floatPackage[0] = relay_board_data.cap_volt;
        floatPackage[1] = relay_board_data.cap_curr;
        hal_stat =
            HAL_CAN_SafeAddTxMessage((uint8_t *)&floatPackage, CAPACITOR_PACKET,
                                     8UL, &TxMailboxCanTask, CAN_RTR_DATA);
        break;
      default:
        // this shouldn't happen
        break;
      }
    }
    osDelay(10);
  }
  /* USER CODE END StartCanRtrTask */
}

/* USER CODE BEGIN Header_StartAdcTask */
/** @brief Function implementing the AdcTask thread. @param argument: Not used
 * @retval None */
/* USER CODE END Header_StartAdcTask */
void StartAdcTask(void *argument) {
  /* USER CODE BEGIN StartAdcTask */
  const float ADC_VOLT_REF = 3.3F / 4096.0F;
  const float CURR_TRANSFER = 0.667F;
  const float VOLT_TRANSFER = 0.107F;
  const float VOLT_TO_CURR_UNI = 12.5F; // A/V
  const float VOLT_TO_CURR_BI = 25.0F;  // A/V
  /* Infinite loop */
  adc1Results[0] = adc1Results[1] = adc1Results[2] = 0;
  adc2Results[0] = adc2Results[1] = adc2Results[2] = 0;
  HAL_ADC_Start_DMA(&hadc1, (uint32_t *)adc1Results, 3);
  HAL_ADC_Start_DMA(&hadc2, (uint32_t *)adc2Results, 3);

  for (;;) {
    if (conversion_completed == 2) {
      relay_board_data.fc_volt = adc1Results[0] * ADC_VOLT_REF / VOLT_TRANSFER;
      relay_board_data.cap_volt = adc1Results[1] * ADC_VOLT_REF / VOLT_TRANSFER;
      relay_board_data.fc_curr =
          ((adc1Results[2] * ADC_VOLT_REF / CURR_TRANSFER) - 0.5) *
          VOLT_TO_CURR_UNI;
      relay_board_data.mtr_curr =
          ((adc2Results[0] * ADC_VOLT_REF / CURR_TRANSFER) - 0.5) *
          VOLT_TO_CURR_UNI;
      relay_board_data.cap_curr =
          ((adc2Results[1] * ADC_VOLT_REF / CURR_TRANSFER) - 2.5) *
          VOLT_TO_CURR_BI;
      relay_board_data.mtr_volt = adc2Results[2] * ADC_VOLT_REF / VOLT_TRANSFER;

      conversion_completed = 0;

      HAL_ADC_Start_DMA(&hadc1, (uint32_t *)adc1Results, 3);
      HAL_ADC_Start_DMA(&hadc2, (uint32_t *)adc2Results, 3);
    }
    osDelay(10);
  }
  /* USER CODE END StartAdcTask */
}

/* USER CODE BEGIN Header_StartIndicateLedTask */
/**
 * @brief Function implementing the IndicateLedTask thread.
 * @param argument: Not used
 * @retval None
 */
/* USER CODE END Header_StartIndicateLedTask */
void StartIndicateLedTask(void *argument) {
  /* USER CODE BEGIN StartIndicateLedTask */
  /* Infinite loop */
  for (;;) {
    switch (rb_state) {
    case RELAY_STBY:
      // Turn off other indicator LEDs
      HAL_GPIO_WritePin(LED_ON_STATE_GPIO_Port, LED_ON_STATE_Pin,
                        GPIO_PIN_RESET);
      HAL_GPIO_WritePin(LED_CHARGE_STATE_GPIO_Port, LED_CHARGE_STATE_Pin,
                        GPIO_PIN_RESET);

      // Flash LED off state
      HAL_GPIO_WritePin(LED_OFF_STATE_GPIO_Port, LED_OFF_STATE_Pin,
                        GPIO_PIN_SET);
      osDelay(500);
      HAL_GPIO_WritePin(LED_OFF_STATE_GPIO_Port, LED_OFF_STATE_Pin,
                        GPIO_PIN_RESET);
      osDelay(500);
      break;
    case RELAY_STRTP:
      // Turn off other indicator LEDs
      HAL_GPIO_WritePin(LED_ON_STATE_GPIO_Port, LED_ON_STATE_Pin,
                        GPIO_PIN_RESET);
      HAL_GPIO_WritePin(LED_CHARGE_STATE_GPIO_Port, LED_CHARGE_STATE_Pin,
                        GPIO_PIN_RESET);

      // Flash faster during startup phase as this section is very short
      HAL_GPIO_WritePin(LED_OFF_STATE_GPIO_Port, LED_OFF_STATE_Pin,
                        GPIO_PIN_SET);
      osDelay(50);
      HAL_GPIO_WritePin(LED_OFF_STATE_GPIO_Port, LED_OFF_STATE_Pin,
                        GPIO_PIN_RESET);
      osDelay(50);
      break;
    case RELAY_CHRGE:
      // Turn off other indicator LEDs
      HAL_GPIO_WritePin(LED_OFF_STATE_GPIO_Port, LED_OFF_STATE_Pin,
                        GPIO_PIN_RESET);
      HAL_GPIO_WritePin(LED_ON_STATE_GPIO_Port, LED_ON_STATE_Pin,
                        GPIO_PIN_RESET);

      // Progressively increase the flashing speed to indicating caps are
      // charging
      if (relay_board_data.cap_volt < 10.0f) {
        HAL_GPIO_WritePin(LED_CHARGE_STATE_GPIO_Port, LED_CHARGE_STATE_Pin,
                          GPIO_PIN_SET);
        osDelay(500 );
        HAL_GPIO_WritePin(LED_CHARGE_STATE_GPIO_Port, LED_CHARGE_STATE_Pin,
                          GPIO_PIN_RESET);
        osDelay(500);
      } else if (relay_board_data.cap_volt < 17.0f) {
        HAL_GPIO_WritePin(LED_CHARGE_STATE_GPIO_Port, LED_CHARGE_STATE_Pin,
                          GPIO_PIN_SET);
        osDelay(250);
        HAL_GPIO_WritePin(LED_CHARGE_STATE_GPIO_Port, LED_CHARGE_STATE_Pin,
                          GPIO_PIN_RESET);
        osDelay(250);
      } else if (relay_board_data.cap_volt <= 25.0f) {

        HAL_GPIO_WritePin(LED_CHARGE_STATE_GPIO_Port, LED_CHARGE_STATE_Pin,
                          GPIO_PIN_SET);
        osDelay(100);
        HAL_GPIO_WritePin(LED_CHARGE_STATE_GPIO_Port, LED_CHARGE_STATE_Pin,
                          GPIO_PIN_RESET);
        osDelay(100);
      }
      break;
    case RELAY_RUN:
      // Turn off other indicator LEDs
      HAL_GPIO_WritePin(LED_CHARGE_STATE_GPIO_Port, LED_CHARGE_STATE_Pin,
                        GPIO_PIN_RESET);
      HAL_GPIO_WritePin(LED_OFF_STATE_GPIO_Port, LED_OFF_STATE_Pin,
                        GPIO_PIN_RESET);

      // Turn on the run LED to indicate driver can apply power
      HAL_GPIO_WritePin(LED_ON_STATE_GPIO_Port, LED_ON_STATE_Pin, GPIO_PIN_SET);
      osDelay(100);
      break;
    default:
      break;
    }
  }
}
/* USER CODE END StartIndicateLedTask */

/* USER CODE BEGIN Header_StartCanDataTask */
/**
 * @brief Function implementing the CanDataTask thread.
 * @param argument: Not used
 * @retval None
 */
/* USER CODE END Header_StartCanDataTask */
void StartCanDataTask(void *argument) {
  /* USER CODE BEGIN StartCanDataTask */
  uint32_t queueData = 0;
  HAL_StatusTypeDef hal_stat;

  const uint32_t CONFIRM_RELAY_CONFIG = 1;
  /* Infinite loop */
  for (;;) {
    if (osMessageQueueGet(canRxDataMsgQueueHandle, &queueData, 0U,
                          osWaitForever) == osOK) {
      switch (queueData) {
      case RELAY_CONFIGURATION_PACKET:
        osMessageQueueGet(canRxDataMsgQueueHandle, &queueData, 0U, 10UL);
        rb_state = queueData;
        hal_stat = HAL_CAN_SafeAddTxMessage((uint8_t *)&CONFIRM_RELAY_CONFIG,
                                            RELAY_CONFIGURATION_PACKET, 4UL,
                                            &TxMailboxCanTask, CAN_RTR_DATA);
        break;
      default:
        break;
      }
      osDelay(10);
    }
  }
  /* USER CODE END StartCanDataTask */
}

/**
 * @brief  Period elapsed callback in non blocking mode
 * @note   This function is called  when TIM1 interrupt took place, inside
 * HAL_TIM_IRQHandler(). It makes a direct call to HAL_IncTick() to increment
 * a global variable "uwTick" used as application time base.
 * @param  htim : TIM handle
 * @retval None
 */
void HAL_TIM_PeriodElapsedCallback(TIM_HandleTypeDef *htim) {
  if (htim->Instance == TIM1) {
    HAL_IncTick();
  }
}
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

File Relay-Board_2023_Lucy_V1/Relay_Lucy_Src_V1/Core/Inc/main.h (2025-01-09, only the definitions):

#define LED_OFF_STATE_Pin GPIO_PIN_0
#define LED_OFF_STATE_GPIO_Port GPIOA
#define LED_CHARGE_STATE_Pin GPIO_PIN_1
#define LED_CHARGE_STATE_GPIO_Port GPIOA
#define LED_ON_STATE_Pin GPIO_PIN_2
#define LED_ON_STATE_GPIO_Port GPIOA
#define FC_VOLT_Pin GPIO_PIN_4
#define FC_VOLT_GPIO_Port GPIOA
#define MOTOR_CURR_Pin GPIO_PIN_5
#define MOTOR_CURR_GPIO_Port GPIOA
#define CAP_VOLT_Pin GPIO_PIN_6
#define CAP_VOLT_GPIO_Port GPIOA
#define CAP_CURR_Pin GPIO_PIN_7
#define CAP_CURR_GPIO_Port GPIOA
#define MTR_VOLT_Pin GPIO_PIN_4
#define MTR_VOLT_GPIO_Port GPIOC
#define FC_CURR_Pin GPIO_PIN_5
#define FC_CURR_GPIO_Port GPIOC
#define DSCHRGE_RELAY_Pin GPIO_PIN_0
#define DSCHRGE_RELAY_GPIO_Port GPIOB
#define RES_RELAY_Pin GPIO_PIN_1
#define RES_RELAY_GPIO_Port GPIOB
#define CAP_RELAY_Pin GPIO_PIN_2
#define CAP_RELAY_GPIO_Port GPIOB
#define MTR_RELAY_Pin GPIO_PIN_10
#define MTR_RELAY_GPIO_Port GPIOB
#define DSCHRGE_LED_Pin GPIO_PIN_12
#define DSCHRGE_LED_GPIO_Port GPIOB
#define RES_LED_Pin GPIO_PIN_13
#define RES_LED_GPIO_Port GPIOB
#define MTR_LED_Pin GPIO_PIN_14
#define MTR_LED_GPIO_Port GPIOB
#define CAP_LED_Pin GPIO_PIN_15
#define CAP_LED_GPIO_Port GPIOB
#define CAN_STBY_Pin GPIO_PIN_7
#define CAN_STBY_GPIO_Port GPIOB

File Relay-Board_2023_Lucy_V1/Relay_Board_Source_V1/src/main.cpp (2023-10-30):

#include "mbed.h"
#include "USBCDC.h"

#include "stm32f4xx.h"
#include "mbed_error.h"

#define DEVICE_USBDEVICE 1

CAN canbus(PA_0, PA_10);
USBCDC cdc;

void SetSysClock();

struct data
{
    float one = 0.12;
    bool two = true;
    uint8_t three = 3;
};

int main()
{   
    struct data mydata;
    canbus.mode(canbus.LocalTest);
    SetSysClock();
    printf("Hello World!");

    while(1)
    {
    };

    return 0;
}


/**
 * Clock configuration below
 */

// clock source is selected with CLOCK_SOURCE in json config
#define USE_PLL_HSE_EXTC 0x8 // Use external clock (ST Link MCO)
#define USE_PLL_HSE_XTAL 0x4 // Use external xtal (X3 on board - not provided by default)
#define USE_PLL_HSI      0x2 // Use HSI internal clock

#define DEBUG_MCO        (1) // Output the MCO1/MCO2 on PA8/PC9 for debugging (0=OFF, 1=ON)


#if ( ((CLOCK_SOURCE) & USE_PLL_HSE_XTAL) || ((CLOCK_SOURCE) & USE_PLL_HSE_EXTC) )
uint8_t SetSysClock_PLL_HSE(uint8_t bypass);
#endif /* ((CLOCK_SOURCE) & USE_PLL_HSE_XTAL) || ((CLOCK_SOURCE) & USE_PLL_HSE_EXTC) */

#if ((CLOCK_SOURCE) & USE_PLL_HSI)
uint8_t SetSysClock_PLL_HSI(void);
#endif /* ((CLOCK_SOURCE) & USE_PLL_HSI) */


/**
  * @brief  Configures the System clock source, PLL Multiplier and Divider factors,
  *               AHB/APBx prescalers and Flash settings
  * @note   This function should be called only once the RCC clock configuration
  *         is reset to the default reset state (done in SystemInit() function).
  * @param  None
  * @retval None
  */

void SetSysClock(void)
{
#if ((CLOCK_SOURCE) & USE_PLL_HSE_EXTC)
    /* 1- Try to start with HSE and external clock */
    if (SetSysClock_PLL_HSE(1) == 0)
#endif
    {
#if ((CLOCK_SOURCE) & USE_PLL_HSE_XTAL)
        /* 2- If fail try to start with HSE and external xtal */
        if (SetSysClock_PLL_HSE(0) == 0)
#endif
        {
#if ((CLOCK_SOURCE) & USE_PLL_HSI)
            /* 3- If fail start with HSI clock */
            if (SetSysClock_PLL_HSI() == 0)
#endif
            {
                {
                    error("SetSysClock failed\n");
                }
            }
        }
    }

    // Output clock on MCO2 pin(PC9) for debugging purpose
#if DEBUG_MCO == 1
    HAL_RCC_MCOConfig(RCC_MCO2, RCC_MCO2SOURCE_SYSCLK, RCC_MCODIV_4);
#endif
}

#if ( ((CLOCK_SOURCE) & USE_PLL_HSE_XTAL) || ((CLOCK_SOURCE) & USE_PLL_HSE_EXTC) )
/******************************************************************************/
/*            PLL (clocked by HSE) used as System clock source                */
/******************************************************************************/
uint8_t SetSysClock_PLL_HSE(uint8_t bypass)
{
    RCC_OscInitTypeDef RCC_OscInitStruct;
    RCC_ClkInitTypeDef RCC_ClkInitStruct;
    RCC_PeriphCLKInitTypeDef PeriphClkInitStruct;

    /* The voltage scaling allows optimizing the power consumption when the device is
       clocked below the maximum system frequency, to update the voltage scaling value
       regarding system frequency refer to product datasheet. */
    __HAL_RCC_PWR_CLK_ENABLE();
    __HAL_PWR_VOLTAGESCALING_CONFIG(PWR_REGULATOR_VOLTAGE_SCALE1);

    /* Get the Clocks configuration according to the internal RCC registers */
    HAL_RCC_GetOscConfig(&RCC_OscInitStruct);

    /* PLL could be already configured by bootlader */
    if (RCC_OscInitStruct.PLL.PLLState != RCC_PLL_ON) {

        // Enable HSE oscillator and activate PLL with HSE as source
        RCC_OscInitStruct.OscillatorType      = RCC_OSCILLATORTYPE_HSE;
        if (bypass == 0) {
            RCC_OscInitStruct.HSEState          = RCC_HSE_ON; // External 8 MHz xtal on OSC_IN/OSC_OUT
        } else {
            RCC_OscInitStruct.HSEState          = RCC_HSE_BYPASS; // External 8 MHz clock on OSC_IN
        }

        RCC_OscInitStruct.PLL.PLLState = RCC_PLL_ON;
        RCC_OscInitStruct.PLL.PLLSource = RCC_PLLSOURCE_HSE;
        RCC_OscInitStruct.PLL.PLLM = 4;             // VCO input clock = 1 MHz (8 MHz / 8)
        RCC_OscInitStruct.PLL.PLLN = 180;           // VCO output clock = 360 MHz (1 MHz * 360)
        RCC_OscInitStruct.PLL.PLLP = RCC_PLLP_DIV2; // PLLCLK = 180 MHz (360 MHz / 2)
        RCC_OscInitStruct.PLL.PLLQ = 5;             //
        RCC_OscInitStruct.PLL.PLLR = 2;             //
        if (HAL_RCC_OscConfig(&RCC_OscInitStruct) != HAL_OK) {
            return 0; // FAIL
        }
    }

    // Activate the OverDrive to reach the 180 MHz Frequency
    if (HAL_PWREx_EnableOverDrive() != HAL_OK) {
        return 0; // FAIL
    }

#if DEVICE_USBDEVICE
    // Select PLLSAI output as USB clock source
    PeriphClkInitStruct.PLLSAI.PLLSAIM = 4;
    PeriphClkInitStruct.PLLSAI.PLLSAIN = 96;
    PeriphClkInitStruct.PLLSAI.PLLSAIP = RCC_PLLSAIP_DIV4;
    PeriphClkInitStruct.PeriphClockSelection = RCC_PERIPHCLK_CLK48;
    PeriphClkInitStruct.Clk48ClockSelection = RCC_CLK48CLKSOURCE_PLLSAIP;
    HAL_RCCEx_PeriphCLKConfig(&PeriphClkInitStruct);
#endif /* DEVICE_USBDEVICE */

    // Select PLL as system clock source and configure the HCLK, PCLK1 and PCLK2 clocks dividers
    RCC_ClkInitStruct.ClockType = RCC_CLOCKTYPE_SYSCLK | RCC_CLOCKTYPE_HCLK | RCC_CLOCKTYPE_PCLK1 | RCC_CLOCKTYPE_PCLK2;
    RCC_ClkInitStruct.SYSCLKSource = RCC_SYSCLKSOURCE_PLLCLK;
    RCC_ClkInitStruct.AHBCLKDivider = RCC_SYSCLK_DIV1; // 180 MHz
    RCC_ClkInitStruct.APB1CLKDivider = RCC_HCLK_DIV4;  //  45 MHz
    RCC_ClkInitStruct.APB2CLKDivider = RCC_HCLK_DIV2;  //  90 MHz
    if (HAL_RCC_ClockConfig(&RCC_ClkInitStruct, FLASH_LATENCY_5) != HAL_OK) {
        return 0; // FAIL
    }

    // Output clock on MCO1 pin(PA8) for debugging purpose
#if DEBUG_MCO == 1
    if (bypass == 0) {
        HAL_RCC_MCOConfig(RCC_MCO1, RCC_MCO1SOURCE_HSE, RCC_MCODIV_2);    // 4 MHz with xtal
    } else {
        HAL_RCC_MCOConfig(RCC_MCO1, RCC_MCO1SOURCE_HSE, RCC_MCODIV_1);    // 8 MHz with external clock (MCO)
    }
#endif

    return 1; // OK
}
#endif /* ((CLOCK_SOURCE) & USE_PLL_HSE_XTAL) || ((CLOCK_SOURCE) & USE_PLL_HSE_EXTC) */
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

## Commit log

2022-04-29 Added Relay Boards, removed meme
    [Relay Board 2018 Parts List.xlsx, Relay_Board_V3.1.brd, Relay_Board_V3.1.sch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]
2022-05-07 Organized branch folders, made changes to schematic
    [Relay Board 2018 Parts List.xlsx, Relay_Board_V3.1.brd, Relay_Board_V3.1.sch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]
2022-05-12 Fixed connection labels
    [Relay_Board_V3.6.brd]
2022-05-12 Removed 5V from signal connections
    [Relay_Board_V3.6.brd, Relay_Board_V3.6.sch]
2022-05-13 Added label for FC Power Board Relay
    [Relay_Board_V3.6.brd, Relay_Board_V3.6.sch]
2022-05-13 Renamed FC Relay net
    [Relay_Board_V3.6.brd, Relay_Board_V3.6.sch]
2023-06-17 Kicad Conversion
    [Relay_Board_V3.6.kicad_pcb]
2023-06-24 Add files via upload
    Relay Board Block Diagram from June 2023
2023-07-19 name change
    [Relay_Board_V3.6.brd, Relay_Board_V3.6.kicad_pcb, Relay_Board_V3.6.kicad_sch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]
2023-08-31 Folder structure layout changes and a begining the board
    [Relay_Board_Lucy_V1.kicad_pcb, Relay_Board_Lucy_V1.kicad_sch, Relay_Board_V3.6.brd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]
2023-08-31 Added mcu
    [mcu.kicad_sch]
2023-09-01 Started laying out relays and current sensors. Working on driving the relays next
    [90A_relay.kicad_sch, Relay_Board_Lucy_V1.kicad_sch, mcu.kicad_sch]
2023-09-16 Updated lower amperage relays
    [90A_relay.kicad_sch, Relay_Board_Lucy_V1.kicad_sch, mcu.kicad_sch]
2023-09-16 some updates
    [90A_relay.kicad_sch, Relay_Board_Lucy_V1.kicad_sch, mcu.kicad_sch]
2023-09-16 Lots of updates to relays
    [30A_relay.kicad_sch, Relay_Board_Lucy_V1.kicad_sch, mcu.kicad_sch]
2023-09-20 Added uart to usb, still needs some work, started prog for mcu
    [30A_relay.kicad_sch, 90A_relay.kicad_sch, Relay_Board_Lucy_V1.kicad_sch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]
2023-09-24 lots of big changes
    [30A_relay.kicad_sch, 90A_relay.kicad_sch, Relay_Board_Lucy_V1.kicad_sch]
2023-10-14 Big changes to relay board
    [0430450612.step, Relay_Board_Lucy_V1.kicad_sch, VP0265540000G.STEP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]
2023-10-14 added a socket
    [PPPC142LFBN-RC.STEP, Relay_Board_Lucy_V1.kicad_sch, mcu.kicad_sch]
2023-10-23 Started the PCB design work
    [30A_relay.kicad_sch, 90A_relay.kicad_sch, Relay_Board_Lucy_V1.kicad_pcb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]
2023-10-28 Board layout is done and routed
    [Relay_Board_Lucy_V1.kicad_pcb, Relay_Board_Lucy_V1.kicad_sch, mcu.kicad_sch]
2023-10-30 Finished the relay board. Once gerbers and drill files are generated we can order from jlc
    [30A_relay.kicad_sch, 430450612.stp, 90A_relay.kicad_sch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]
2023-11-05 Started work on the BOM file and I updated the lower current relays to work with 50A models
    [30A_relay.kicad_sch, 90A_relay.kicad_sch, Relay_Board_Lucy_V1.kicad_pcb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]
2023-11-06 updated, created gerbers, created p&p, created BOM's
    [30A_relay.kicad_sch, 629105150521_Download_STP_629105150521_rev1.stp, 90A_relay.kicad_sch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]
2023-11-12 Added optocouplers and reworked relay controls
    [30A_relay.kicad_sch, 90A_relay.kicad_sch, Relay_Board_Lucy_V1.kicad_pcb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]
2023-11-12 Made the new gerbs and bom files and ordered the pcb
    [30A_relay.kicad_sch, 90A_relay.kicad_sch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]
2024-01-13 Started the code for the relay board
2024-02-22 ADC working properly, able to receive relay configuration commands and respond. Succesfully transmitting cap voltage as well
2024-04-25 This version of the boards/code was used at competition

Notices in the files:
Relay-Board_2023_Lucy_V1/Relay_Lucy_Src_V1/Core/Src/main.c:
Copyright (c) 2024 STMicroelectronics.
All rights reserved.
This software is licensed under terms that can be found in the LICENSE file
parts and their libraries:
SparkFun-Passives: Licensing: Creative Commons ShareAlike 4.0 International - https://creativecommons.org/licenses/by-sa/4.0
